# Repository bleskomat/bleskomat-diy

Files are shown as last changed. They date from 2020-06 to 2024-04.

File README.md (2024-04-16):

# Bleskomat DIY

The Bleskomat DIY is an offline Bitcoin Lightning Network ATM which accepts coins and pays-out bitcoin. It's a great educational tool to give others a practical first experience with Bitcoin's Lightning Network.

You can buy the [Bleskomat DIY kit](https://shop.bleskomat.com/product/bleskomat-diy-kit/) from the official Bleskomat shop - includes all the parts needed to build the project. Alternatively, you can find all the components and equipment needed from various other sources - see [Parts Suppliers](#parts-suppliers).

The Bleskomat DIY must be paired with a server to facilitate Lightning Network payments on its behalf; see the options below:
* [Bleskomat Platform](https://platform.bleskomat.com) - non-custodial, requires a monthly subscription
* [bleskomat-server](https://github.com/bleskomat/bleskomat-server) - non-custodial, open-source, self-hosted solution
* [lnbits](https://github.com/lnbits/lnbits-legend) via the Bleskomat extension - open-source, self-hosted and possible to use custodial instances hosted by others; public instances of lnbits:
	* [legend.lnbits.com](https://legend.lnbits.com) - unstable, don't leave funds on this instance for very long

The rest of this document details the hardware and software requirements, how to build the hardware yourself, and instructions for compiling and uploading the firmware from source.

* [Requirements](#requirements)
	* [Hardware Requirements](#hardware-requirements)
		* [Parts Suppliers](#parts-suppliers)
	* [Software Requirements](#software-requirements)
* [Building the Hardware Device](#building-the-hardware-device)
	* [Prepare the breadboards](#prepare-the-breadboards)
		* [ESP32 devkit pinout](#esp32-devkit-pinout)
	* [Wiring the Power Supply](#wiring-the-power-supply)
		* [Optionally power the ESP32 devkit via 5V pin](#optionally-power-the-esp32-devkit-via-5v-pin)
	* [Wiring the TFT Display](#wiring-the-tft-display)
		* [Wiring the SD card slot](#wiring-the-sd-card-slot)
	* [Wiring the button](#wiring-the-button)
	* [Wiring the Coin Acceptor](#wiring-the-coin-acceptor)
		* [Wiring the DG600F](#wiring-the-dg600f)
		* [Wiring the HX616](#wiring-the-hx616)
	* [Wiring the Bill Acceptor](#wiring-the-bill-acceptor)
* [Configure and Train Coin Acceptor](#configure-and-train-coin-acceptor)
	* [Configure and Train the DG600F](#configure-and-train-the-dg600f)
	* [Configure and Train the HX616](#configure-and-train-the-hx616)
* [Configure Bill Acceptor](#configure-bill-acceptor)
* [Installing Libraries and Dependencies](#installing-libraries-and-dependencies)
* [Configure Firmware Build Flags](#configure-firmware-build-flags)
* [Compiling and Uploading to Device](#compiling-and-uploading-to-device)
* [Configuring the Device](#configuring-the-device)
	* [List of Configuration Options](#list-of-configuration-options)
	* [Browser-Based Configuration Tool](#browser-based-configuration-tool)
	* [Command-Line Configuration Tool](#command-line-configuration-tool)
	* [Hard-Coded Configuration](#hard-coded-configuration)
	* [Configuration via SD Card](#configuration-via-sd-card)
* [Changelog](#changelog)
* [Support](#support)
* [License](#license)
* [Trademark](#trademark)

## Requirements

This section includes information about the software and hardware requirements needed to build this project.

### Hardware Requirements

Basic components/equipment needed to build your own Bleskomat DIY:
* 2 x breadboard (400-pin)
* Jumper wires (M-M)
* Jumper wires (M-F)
* ESP32 Devkit
* Coin Acceptor - DG600F or HX616
* 1.8" TFT display
* Button
* 10k ohm resistor
* DC 5.5/2.1 mm DIP adapter
* 12V DC power adaptor with \~1A
* Standard USB to micro USB cable
* Multimeter

Optional components/equipment:
* Soldering iron
* 2.54 mm pins
* To power the ESP32 devkit from the 12V DC power supply:
	* XL4005 step-down converter
	* USB (F) adapter
	* Alternatively, you could use a USB car charger which includes both a step-down converter and USB (F) output
* If you wish to configure your Bleskomat via SD card:
	* Micro SD card with macro adapter

See the [Parts Suppliers](#parts-suppliers) section below for links to suppliers for each component/equipment.

#### Parts Suppliers

Below are parts lists based on geographic location:

* [Czech Republic](docs/parts-lists/czech-republic.md)
* [United Kingdom](docs/parts-lists/uk.md)
* [USA](docs/parts-lists/usa.md)

If you'd like to add your own list, please create a pull-request using [this template](docs/parts-lists/TEMPLATE.md) as a guide. Links with referral codes will not be accepted.

### Software Requirements

* [make](https://www.gnu.org/software/make/)
* [PlatformIO Core (CLI)](https://docs.platformio.org/en/latest/core/)
	* Version 6 or newer
	* Only the CLI ("Core") is required

## Building the Hardware Device

Before proceeding, be sure that you have all the project's [hardware requirements](#hardware-requirements).

Step-by-step build process for the hardware device.

### Prepare the breadboards

One breadboard is not large enough to accommodate all the pins of the ESP32 devkit due to the width of the devkit. This is why we recommend to connect two breadboards together.

Remove one of the power rails from one of the breadboards. Use the notches on the sides of the breadboards to connect them together length-wise.

Insert the ESP32 devkit into the pin holes of the new, combined breadboard.

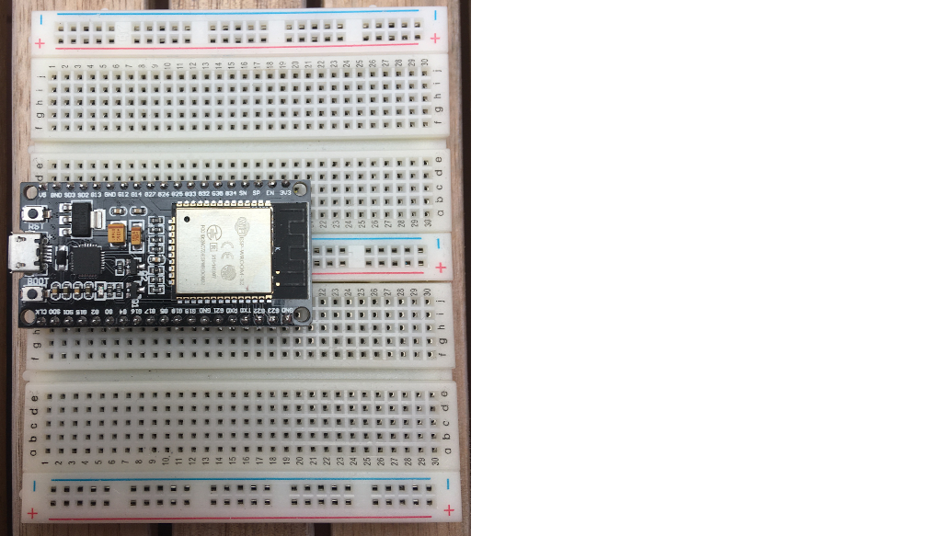
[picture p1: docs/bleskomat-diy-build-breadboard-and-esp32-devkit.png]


Familiarize yourself with the ESP32 devkit's pinout reference below.

#### ESP32 devkit pinout

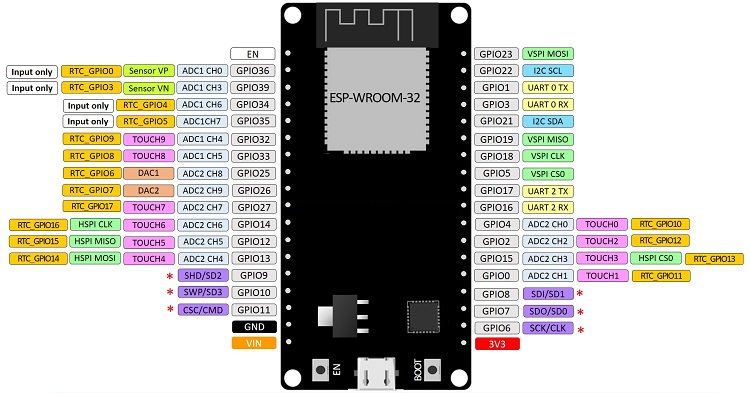
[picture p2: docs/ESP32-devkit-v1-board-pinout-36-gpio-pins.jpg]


### Wiring the Power Supply

The first step to building the device is wiring the power supply. If already plugged in, __unplug__ the 12V DC power supply now. Connect the DC 5.5/2.1 end of the power supply to the DIP adapter. The positive (+) pins should be the power pins and the negative (-) pins should be the ground. You can use your multimeter to check in case you want to be extra safe:
* Plug-in the power supply to electricity
* Turn on your multimeter and set it to measure voltage in the appropriate range (probably 20V)
* Touch the __red__ lead of your multimeter to one of the positive pins
* Touch the __black__ lead of your multimeter to one of the negative pins
* If you see a negative voltage reading, swap the leads between the two wires
* The pin touched by the __black__ lead is the ground ("GND")
* The pin touched by the __red__ lead is the hot wire ("DC12V")
* Unplug the power supply again

Use a pair of M-F jumper wires to connect the DC 5.5/2.1 DIP adapter to one of the breadboard's power rails. Negative to negative, positive to positive. This rail will be your 12V DC power (positive) and the common ground (negative).

#### Optionally power the ESP32 devkit via 5V pin

If you'd like to make your Bleskomat build a little bit more portable, you can power the ESP32 devkit via its 5V pin. To do this you will need the XL4005 (or equivalent) step-down converter and the USB (F) adapter. Note that powering the ESP32 devkit via its micro USB port requires a regulated voltage of approximately 5V.

It's also possible to use a USB car charger in case you have an extra one lying around.

Connect the step-down converter's input pins to the 12V DC power rail and common ground using (M-F) jumper wires. Use a multimeter to measure the voltage at the out pins. In the case of the XL4005, use a small screwdriver to turn the screw on the little blue box. Turning the screw counter clockwise should lower the voltage, turning it the opposite direction should increase the voltage. Once you have the voltage set to 5V, connect the out pins to the center power rails of the breadboard. This will be your 5V DC power rail.

Use a soldering iron to solder four 2.54 mm pins to the USB (F) DIP adapter. Insert the pins directly into the breadboard wherever you have space available. Using (M-M) jumper wires, connect the negative and positive pins of the USB (F) DIP adapter to the 5V DC power rail.

Connect the negative pin of the 5V DC power rail to the negative of the 12V DC power rail to ensure that they share a common ground. This is important because without a common ground shared between the coin acceptor and ESP32 devkit, the ESP32 will not receive a clean signal from the coin acceptor.

Use a standard USB to micro USB cable to connect the USB (F) DIP adapter to the ESP32 devkit.

There are other options when powering the ESP32 - e.g via the 3.3V pin or the 5V/VIN pin. You should __never__ power the ESP32 via more than one of these options at the same time. For example, do not power the ESP32 via its 3.3V pin while also connecting the ESP32 via USB to your computer. This can damage the ESP32 and possibly also your computer.

### Wiring the TFT Display

Insert the pins of the TFT display module into the breadboard where you have space available.

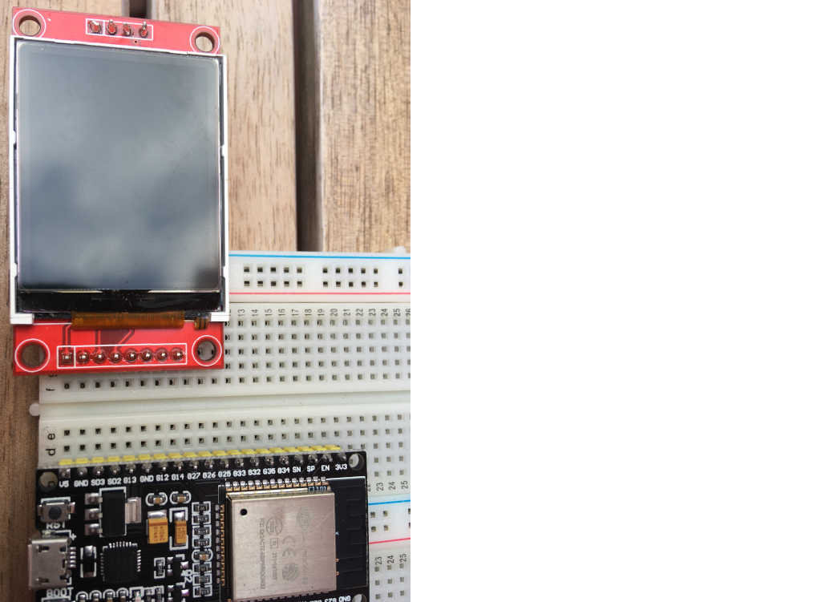
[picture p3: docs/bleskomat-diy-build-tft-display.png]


Use the table below to connect the ESP32 devkit to the TFT display module.

|  ESP32 | TFT |
|---|---|
| VIN (V5) | VCC |
| GND | GND |
| GPIO22 | CS |
| GPIO4 | RESET (RST) |
| GPIO2 | AO (RS) |
| GPIO23 | SDA |
| GPIO18 | SCK (CLK) |
| 3V3 | LED (NC) |

Notes on pin naming:
* There are boards where `GPIXXX` are marked as `GXX` instead of `DXX`.
* The `G23` may be there **twice** - the correct one is next to `GND`.
* Some boards have typos so a bit of guess-and-check is necessary sometimes.

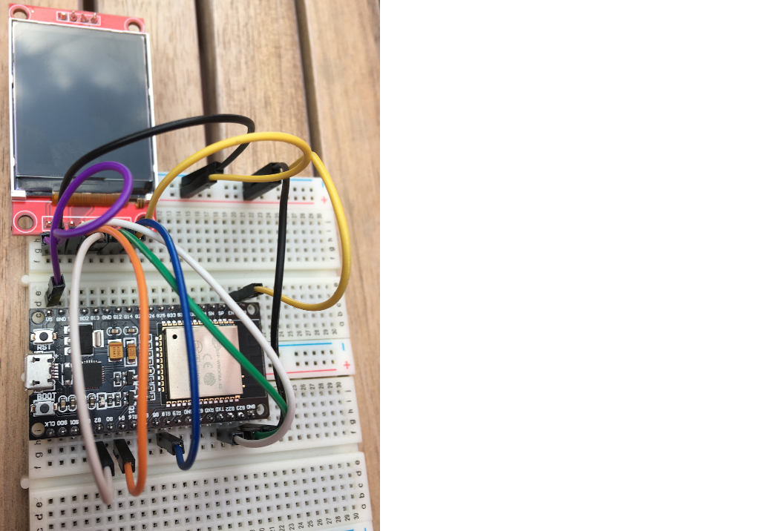
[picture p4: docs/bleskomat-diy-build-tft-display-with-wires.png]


Refer to the [ESP32 devkit pinout](#esp32-devkit-pinout) for help identifying the pins on your ESP32.

#### Wiring the SD card slot

This step is only needed if you would like to configure your Bleskomat via an SD card.

The TFT display includes an SD card slot. The pins are located above the screen and not soldered to the module by default but the pins can be added. The table of mappings is the following:

| ESP32  | TFT |
|---|---|
| GPIO15 | SD_CS |
| GPIO13 | SD_MOSI |
| GPIO12 | SD_MISO |
| GPIO14 | SD_SCK  |

Refer to the [ESP32 devkit pinout](#esp32-devkit-pinout) for help identifying the pins on your ESP32.

### Wiring the button

Insert button pins into the breadboard wherever you have space available. Typically, its best to place the button at the center of a breadboard (over the gap).

Connect the button using the following table as a guide:

| ESP32 | Button |
|---|---|
| VIN (V5) | left pin  |
| GPIO33 | right pin |

Connect the right pin of the button to GND with a 10k ohm resistor.

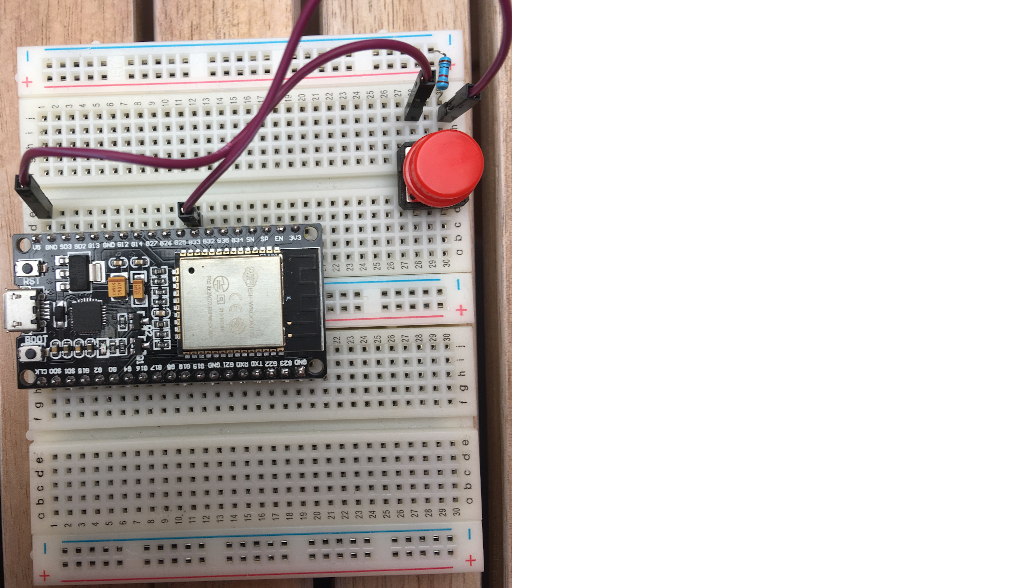
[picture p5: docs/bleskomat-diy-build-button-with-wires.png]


Refer to the [ESP32 devkit pinout](#esp32-devkit-pinout) for help identifying the pins on your ESP32.

### Wiring the Coin Acceptor

This project supports two possible coin acceptors - the DG600F and the HX616. The DG600F is more expensive, but is easier to configure and more reliable.

#### Wiring the DG600F

| ESP32 | DG600F | Power Supply  |
|---|---|---|
| GPIO1 (TX0) | INHIBIT  | |
| | COUNTER  | |
| | GND | - Ground |
| GPIO3 (RX0) | SIGNAL | |
| | DC12V | + 12V DC |

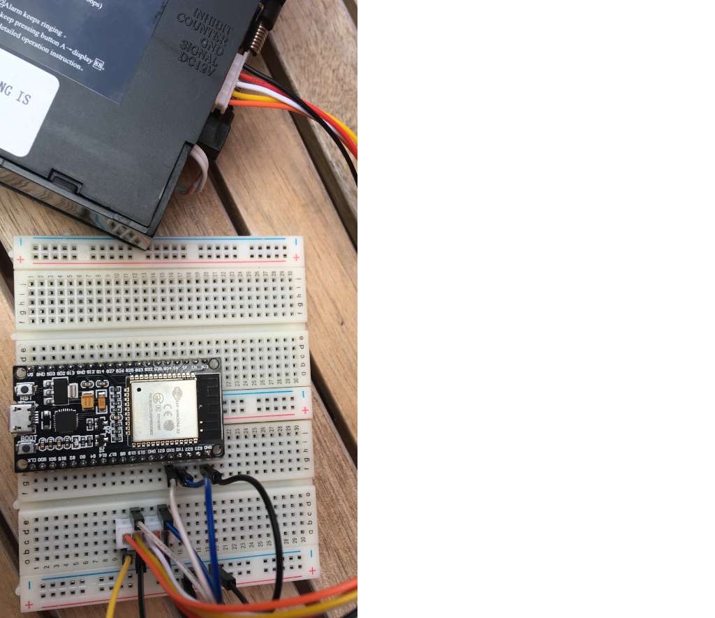
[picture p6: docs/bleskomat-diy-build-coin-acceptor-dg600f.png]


Refer to the [ESP32 devkit pinout](#esp32-devkit-pinout) for help identifying the pins on your ESP32.

#### Wiring the HX616

| ESP32 | HX616 | Power Supply  |
|---|---|---|
| | DC12V | + 12V DC |
| GPIO3 (RX0) | COIN | |
| | GND | - Ground |

Refer to the [ESP32 devkit pinout](#esp32-devkit-pinout) for help identifying the pins on your ESP32.

### Wiring the Bill Acceptor

This project supports the NV10 (USB+) and NV9 bill acceptors. The SIO protocol is used to communicate with the bill acceptor unit.

|  ESP32 | NV10/NV9 | Power Supply  |
|---|---|---|
| GPIO16 | 1 (Tx) | |
| GPIO17 | 5 (Rx) | |
| | 16 | - Ground |
| | 15 | + 12V DC |

Refer to the [ESP32 devkit pinout](#esp32-devkit-pinout) for help identifying the pins on your ESP32.

## Configure and Train Coin Acceptor

This project supports two possible coin acceptors - the DG600F and the HX616.

### Configure and Train the DG600F

Physical switches on the DG600F should set as follows:

| Switch | State |
|---|---|
| 1 (Port Level) | Down (NO) |
| 2 (Security) | Down (Normal) |
| 3 (Transmitting) | Up (RS232) |
| 4 (Inhibiting) | Down (> +3V)  |



Open the [DG600F manual](docs/DG600F-Coin-Acceptor-Technical-Manual.pdf) to "Coin Acceptor Parameters Setting" on page 18. Set the parameters as follows:

| Parameter | Description | Value | Meaning |
|---|---|---|---|
| A1 | machine charge amount | 01 | min. coin value before data sent |
| A2 | serial output signal pulse-width | 01 | 25ms / 9600 bps (RS232 baud rate) |
| A3 | faulty alarm option | 01 | (rings only one time) |
| A4 | serial port RS232 signal length  | 03 | 3 bytes: 0xAA, coin value, XOR of prev two bytes |
| A5 | serial port output | 01 | output to serial pin |

To train the coin acceptor, have a look at "Coin Parameters Setting" on page 16 of the [DG600F manual](docs/DG600F-Coin-Acceptor-Technical-Manual.pdf). Be sure to set the "coin value" for each coin in series, incremented by 1. For example:
* 0.05 EUR = 1 coin value
* 0.10 EUR = 2 coin value
* 0.20 EUR = 3 coin value
* 0.50 EUR = 4 coin value
* 1.00 EUR = 5 coin value
* 2.00 EUR = 6 coin value

Then set the `coinValues` configuration equal to `0.05,0.10,0.20,0.50,1,2`. For example, in the bleskomat.conf:
```
coinValues=0.05,0.10,0.20,0.50,1,2
```

### Configure and Train the HX616

There are two switches on the back of the HX616 coin acceptor:
* "NO" (normally open) / "NC" (normally closed) - This should be set to "NO"
* "Fast" / "Medium" / "Slow" - This should be set to "Fast"

An instruction sheet is included with the coin acceptor that will guide you through the training process:

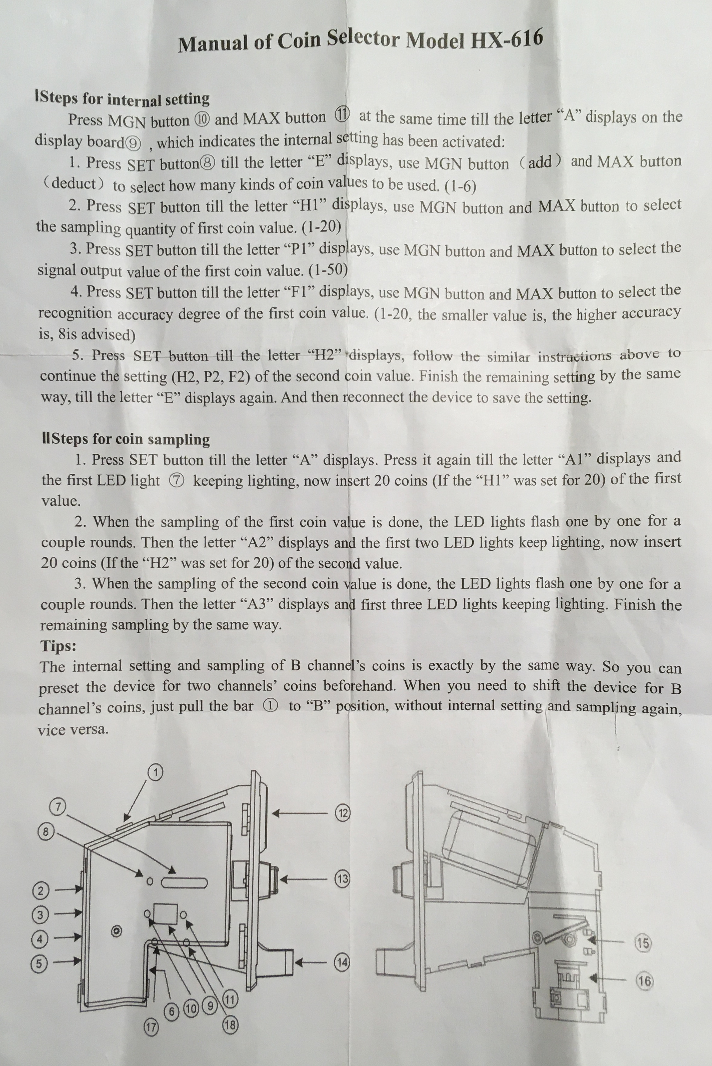
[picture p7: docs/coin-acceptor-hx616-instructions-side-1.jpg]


| PANEL  | Meaning |
|---|---|
| E | number of coin values |
| Hn | sampling quantity of coin n |
| Pn | signal output value of coin n |
| Fn | recognition accuracy of coin n (8 advised)  |
| A | training the acceptor |
| An | start inserting coins for coin n |

Press ADD + MINUS to get to the setting menu for Hn, Pn, Fn. Then press SET to swap between possibilities. To change the option press ADD or MINUS to select the desired value and confirm with SET.

Press SET to enter the training menu (A appears on the panel). After pressing SET again you can start inserting the coins.

If training the HX616 to accept EUR coins, you can set the `coinValueIncrement` equal to `0.05`. For example, in bleskomat.conf:
```
coinValueIncrement=0.05
```

## Configure Bill Acceptor

Please refer to the following user manuals for detailed instructions regarding how to configure the NV10 (USB+) or NV9 bill acceptors:
* [NV10 User Manual](docs/NV10-User-Manual-v1.1.pdf)
* [NV9 User Manual](docs/NV9-User-Manual-v1.1.pdf)

## Installing Libraries and Dependencies

Before proceeding, be sure that you have all the project's [software requirements](#software-requirements).

Use make to install libraries and dependencies needed to build the firmware:
```bash
make install
```
* The firmware's dependencies are defined in its platformio.ini file located at `./platformio.ini`

If while developing you need to install a new library, use the following as a guide:
```bash
platformio lib install LIBRARY_NAME[@VERSION]
```
You can find PlatformIO's libraries repository [here](https://platformio.org/lib).

## Configure Firmware Build Flags

There are several build flags that can be changed in file platformio.ini file located at `./platformio.ini` before the firmware is compiled. If you follow the wire mappings in this readme file, then you most likely do not need to change any flags.

## Compiling and Uploading to Device

To compile the firmware (without uploading to a device):
```bash
make compile
```

To compile and upload to your device:
```bash
make upload DEVICE=/dev/ttyUSB0
```
The device path for your operating system might be different. If you receive a "Permission denied" error about `/dev/ttyUSB0` then you will need to set permissions for that file on your system:
```bash
sudo chown $USER:$USER /dev/ttyUSB0
```

To open the serial monitor:
```bash
make monitor DEVICE=/dev/ttyUSB0
```
Again the device path here could be different for your operating system.

## Configuring the Device

It is possible to configure the device via the following methods:
* [Browser-Based Configuration Tool](#browser-based-configuration-tool)
* [Command-Line Configuration Tool](#command-line-configuration-tool)
* [Hard-Coded Configuration](#hard-coded-configuration)
* [Configuration via SD Card](#configuration-via-sd-card)

### List of Configuration Options

The following is a list of possible configuration options for the Bleskomat DIY:
* `apiKey.id` - The API key ID of the device. This is needed by the server to verify signatures created by the device.
* `apiKey.key` - The API key secret that is used to generate signatures.
* `apiKey.encoding` - The explicit encoding of the API key secret. This can be "hex", "base64", or empty-string (e.g "") to mean no encoding. When generating a new API key on the server, it will store the encoding along with the ID and secret.
* `callbackUrl` - The LNURL server base URL plus endpoint path. Example:
	* `https://p.bleskomat.com/u`
* `shorten` - Whether or not to shorten the LNURL; see the [lnurl-node module](https://github.com/chill117/lnurl-node#signed-lnurls) for more details.
* `uriSchemaPrefix` - The URI schema prefix for LNURLs generated by the device. It has been discovered that some wallet apps mistakenly only support lowercase URI schema prefixes. Uppercase is better because when encoded as a QR code, the generated image is less complex and so easier to scan. Set this config to empty-string (e.g `uriSchemaPrefix=`) to not prepend any URI schema prefix.
* `fiatCurrency` - The fiat currency symbol for which the device is configured; see [ISO 4217](https://en.wikipedia.org/wiki/ISO_4217).
* `fiatPrecision` - The number of digits to the right of the decimal point when rendering fiat currency amounts.
* `billValues` - The value of bills for which the bill acceptor has been configured. Each value separated by a comma. Integers and floating point (decimal) values are accepted. Examples:
	* CZK: `100,200,500,1000,2000,5000`
	* EUR: `5,10,20,50,100,200,500`
* `billTxPin` - The GPIO connected to the NV10/NV9's Tx pin.
* `billRxPin` - The GPIO connected to the NV10/NV9's Rx pin.
* `billBaudRate` - The baud rate of the SIO protocol communication with the NV10/NV9. This value will be `300` or `9600`.
* `coinValues` - For the DG600F coin acceptor. The value of coins for which the coin acceptor has been configured. Each value separated by a comma. Integers and floating point (decimal) values are accepted. For example, when trained with EUR coins this configuration could be set to `0.05,0.10,0.20,0.50,1,2`.
* `coinValueIncrement` - For the HX616 coin acceptor, which communicates via pulses to the ESP32. The value here will determine how much fiat value each pulse represents. For example, when trained with EUR coins this value could be `0.05` with the following number of pulses set for each coin denomination:
	* 0.05 EUR = 1 pulse
	* 0.10 EUR = 2 pulses
	* 0.20 EUR = 4 pulses
	* 0.50 EUR = 10 pulses
	* 1.00 EUR = 20 pulses
	* 2.00 EUR = 40 pulses
* `coinSignalPin` - The GPIO connected to the HX616's "COIN" pin or DG600F's "SIGNAL" pin.
* `coinInhibitPin` - The GPIO connected to the DG600F's "INHIBIT"
* `coinBaudRate` - The baud rate for serial communication with the DG600F
* `coinAcceptorType` - "hx616" or "dg600f"
* `buttonPin` - The GPIO connected to the button
* `buttonDelay` - The number of milliseconds to wait before pressing the button can clear the QR code
* `buttonDebounce` - The number of milliseconds of debounce to prevent flickering button press/release
* `tftRotation` - The orientation of the TFT display. This is useful to allow different positions of the display. The possible rotation values are:
	* 0 = 0 degrees
	* 1 = 90 degrees
	* 2 = 180 degrees
	* 3 = 270 degrees
* `logLevel` - Possible values:
	* `trace` - everything
	* `debug`
	* `info` - default
	* `warn`
	* `error`
	* `none` - nothing

### Browser-Based Configuration Tool

The Bleskomat Platform provides a [browser-based configuration tool](https://platform.bleskomat.com/serial) to upload pre-built device firmware, view real-time log output, update device configurations, run JSON-RPC serial commands, and more.

### Command-Line Configuration Tool

It is also possible to use the [bleskomat-cli](https://github.com/bleskomat/bleskomat-cli) command-line utility to communicate with a Bleskomat hardware device via JSON-RPC over serial API. Please refer to that project's readme for installation and usage information.

### Hard-Coded Configuration

Hard-coded configurations can be set by modifying the source file [config.cpp](https://github.com/bleskomat/bleskomat-diy/blob/master/src/config.cpp#L196).

Each time you make changes to the hard-coded configurations, you will need to re-compile and flash the ESP32's firmware.

### Configuration via SD Card

First you will need to format the SD card with the FAT32 filesystem.

Create a new file named `bleskomat.conf` at the root of the SD card's filesystem.

The following is an example `bleskomat.conf` file:
```
apiKey.id=6d830ddeb0
apiKey.key=b11cd6b002916691ccf3097eee3b49e51759225704dde88ecfced76ad95324c9
apiKey.encoding=hex
callbackUrl=https://p.bleskomat.com/u
shorten=true
uriSchemaPrefix=
fiatCurrency=EUR
fiatPrecision=2
coinValues=0.05,0.10,0.20,0.50,1,2
coinValueIncrement=0.05
coinSignalPin=3
coinInhibitPin=1
coinBaudRate=9600
coinAcceptorType=hx616
buttonPin=33
buttonDelay=5000
buttonDebounce=100
tftRotation=2
logLevel=info
```

## Changelog

See [CHANGELOG.md](https://github.com/bleskomat/bleskomat-diy/blob/master/CHANGELOG.md)

## Support

Need some help? Join us in the official [Telegram group](https://t.me/bleskomat) or send us an email at [support@bleskomat.com](mailto:support@bleskomat.com) and we will try our best to respond in a reasonable time. If you have a feature request or bug to report, please [open an issue](https://github.com/bleskomat/bleskomat-diy/issues) in this project repository.

## License

The project is licensed under the [GNU General Public License v3 (GPL-3)](https://tldrlegal.com/license/gnu-general-public-license-v3-(gpl-3)):
> You may copy, distribute and modify the software as long as you track changes/dates in source files. Any modifications to or software including (via compiler) GPL-licensed code must also be made available under the GPL along with build & install instructions.

## Trademark

"Bleskomat" is a registered trademark. You are welcome to hack, fork, build, and use the source code and instructions found in this repository. However, the right to use the name "Bleskomat" with any commercial products or services is withheld and reserved for the trademark owner.

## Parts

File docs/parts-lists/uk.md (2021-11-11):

# Parts List for United Kingdom

List of recommended electronics parts suppliers in UK:
* [Hobbytronics](https://www.hobbytronics.co.uk/)
* [RobotShop](https://www.robotshop.com/uk/)
* [AdaptorsRUs](https://www.acadaptorsrus.co.uk/)
* [RSComponents](https://uk.rs-online.com/web/)
* [HobbyComponents](https://hobbycomponents.com/)
* [PicStop](https://www.picstop.co.uk/)

Basic components/equipment needed to build your own Bleskomat (DIY) ATM:
* 2 x [Breadboard (400-pin)](https://www.hobbytronics.co.uk/breadboard-400)
* [Connecting cables (M-M)](https://www.hobbytronics.co.uk/jumper-wires-mm-6in)
* [Connecting cables (M-F)](https://www.hobbytronics.co.uk/jumper-wires-mf-6in)
* [ESP32 Devkit](https://www.robotshop.com/uk/esp32-c3-devkitc-02-development-board.html)
* [DG600F Coin Acceptor](https://www.robotshop.com/uk/programmable-coin-acceptor.html)
* [1.8" TFT display](https://www.robotshop.com/uk/sparkfun-18-128x160-tft-lcd-breakout-board.html)
* [Button](https://www.hobbytronics.co.uk/tactile-button-assortment)
* [10k ohm resistor](https://www.robotshop.com/uk/resistor-10k-ohm-1-4-watt-pth-20pk.html)
* [DC 5.5/2.1 mm DIP adapter](https://www.ebay.co.uk/itm/DC-Power-Jack-with-DIP-Adapter-Barrel-Type-Socket-Breakout-Board-DC-Power-Supply-/114944864538)
* [12V DC power adaptor with \~1A](https://www.acadaptorsrus.co.uk/12v-1a-1-amp-mains-ac-dc-adaptor-power-supply-for-yeskamo-cctv-system-uk-plug/) or [this one](https://uk.rs-online.com/web/p/ac-dc-adapters/1753303/)
* [Standard USB to micro USB cable](https://uk.rs-online.com/web/p/usb-cables/1828869)
* [Multimeter](https://www.hobbytronics.co.uk/digital-multimeter-basic)

Optional components/equipment:
* [Soldering iron](https://www.hobbytronics.co.uk/test-equipment/soldering_tools/antex-soldering-iron-xs25)
* [2.54 mm pins](https://hobbycomponents.com/connectors/656-ra-40-way-01-breakable-male-pin-headers)
* To power the ESP32 devkit from the 12V DC power supply:
	* [DC-DC step-down converter](https://www.robotshop.com/uk/step-down-dc-dc-power-converter-25w.html)
	* [USB (F) adapter](https://www.hobbytronics.co.uk/cables-connectors/usb-connectors/usb-type-a-socket)
	* Alternatively, you could use a USB car charger which includes both a step-down converter and USB (F) output
* If you wish to configure your Bleskomat via SD card:
	* [Micro SD card ...](https://www.picstop.co.uk/microsd-sdhc/sandisk-ultra-micro-sdhc-memory-card-98mbs-class-10-for-android-16gb.html)
	* [... with macro adapter](https://www.picstop.co.uk/card-adapters/micro-sd-card-adapter.html)

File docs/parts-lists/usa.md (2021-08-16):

# Parts List for USA

Recommended websites to search for parts:
* [digikey](https://www.digikey.com/en/products)
* [mouser](https://www.mouser.com/)

Basic components/equipment needed to build your own Bleskomat (DIY) ATM:
* 2 x [Breadboard (400-pin)](https://www.adafruit.com/product/4539)
* [Jumper wires (M-M)](https://www.adafruit.com/product/1956)
* [Jumper wires (M-F)](https://www.adafruit.com/product/825)
* ESP32 Devkit:
	* [digikey](https://www.digikey.com/en/products/detail/espressif-systems/ESP32-DEVKITC-32E/12091810)
	* [adafruit](https://www.adafruit.com/product/4693)
* DG600F Coin Acceptor:
	* [sparkfun](https://www.sparkfun.com/products/11636)
	* [alibaba](https://www.alibaba.com/trade/search?fsb=y&IndexArea=product_en&CatId=&SearchText=DG600F)
* 1.8" (128 x 160 pixel) TFT display
* [Button](https://www.adafruit.com/product/1009)
* [10k ohm resistor](https://www.adafruit.com/product/2784)
* [DC 5.5/2.1 mm DIP adapter](https://www.adafruit.com/product/798)
* [12V DC power adaptor with \~1A](https://www.adafruit.com/product/798)
* Standard USB to micro USB cable
* [Multimeter](https://www.adafruit.com/product/2034)

Optional components/equipment:
* [Soldering iron](https://www.adafruit.com/product/180)
* 2.54 mm pins
* To power the ESP32 devkit from the 12V DC power supply:
	* XL4005 step-down converter
	* USB (F) adapter
	* Alternatively, you could use a USB car charger which includes both a step-down converter and USB (F) output
* If you wish to configure your Bleskomat via SD card:
	* Micro SD card with macro adapter

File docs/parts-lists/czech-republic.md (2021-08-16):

# Parts List for Czech Republic

List of recommended electronics parts suppliers in Czech Republic:
* [laskarduino.cz](https://www.laskarduino.cz)
* [alza.cz](https://www.alza.cz)
* [gme.cz](https://www.gme.cz/)

Basic components/equipment needed to build your own Bleskomat (DIY) ATM:
* 2 x [Breadboard (400-pin)](https://www.laskarduino.cz/nepajive-kontaktni-pole-400-pinu--bile/)
* [Jumper wires (M-M)](https://www.laskarduino.cz/dupont-propojovaci-kabely-40ks-m-m-samec-samec--10cm-/)
* [Jumper wires (M-F)](https://www.laskarduino.cz/dupont-propojovaci-kabely-40ks-m-f-samec-samice--10cm-/)
* [ESP32 Devkit](https://www.laskarduino.cz/iot-esp-32s-2-4ghz-dual-mode-wifi-bluetooth-rev-1--cp2102/)
* DG600F Coin Acceptor:
	* _No known local part supplier_
	* Suggestions:
		* [Alibaba.com](https://www.alibaba.com/trade/search?fsb=y&IndexArea=product_en&CatId=&SearchText=DG600F)
		* [Sparkfun.com](https://www.sparkfun.com/products/11636)
* [1.8" TFT display](https://www.laskarduino.cz/128x160-barevny-lcd-tft-displej-1-8--spi/)
* [Button](https://www.laskarduino.cz/mikrospinac-tc-1212t-12x12x7-3mm/)
* [10k ohm resistor](https://www.laskarduino.cz/futaba-1-4w-odpor-10k-5/)
* [DC 5.5/2.1 mm DIP adapter](https://www.laskarduino.cz/dc-5-5-2-1mm-na-dip-adapter-led/)
* [12V DC power adaptor with \~1A](https://www.laskarduino.cz/napajeci-adapter-sitovy-1000ma-5-5-2-1-mm-12v/)
* [Standard USB to micro USB cable](https://www.laskarduino.cz/50cm-microusb-kabel/)
* [Multimeter](https://www.gme.cz/digitalni-multimetr-proskit-mt-1210)

Optional components/equipment:
* [Soldering iron](https://www.gme.cz/pajeci-stanice-48w-ss-203b)
* [2.54 mm pins](https://www.laskarduino.cz/dupont-40pin-2-54-mm-pinovy-pas--pravy-uhel/)
* To power the ESP32 devkit from the 12V DC power supply:
	* [XL4005 step-down converter](https://www.laskarduino.cz/step-down-menic-s-xl4005/)
	* [USB (F) adapter](https://www.laskarduino.cz/usb-f-na-dip-adapter/)
	* Alternatively, you could use a USB car charger which includes both a step-down converter and USB (F) output
* If you wish to configure your Bleskomat via SD card:
	* [Micro SD card with macro adapter](https://www.alza.cz/sandisk-microsdhc-16gb-ultra-android-class-10-uhs-i-d5127467.htm?o=2)

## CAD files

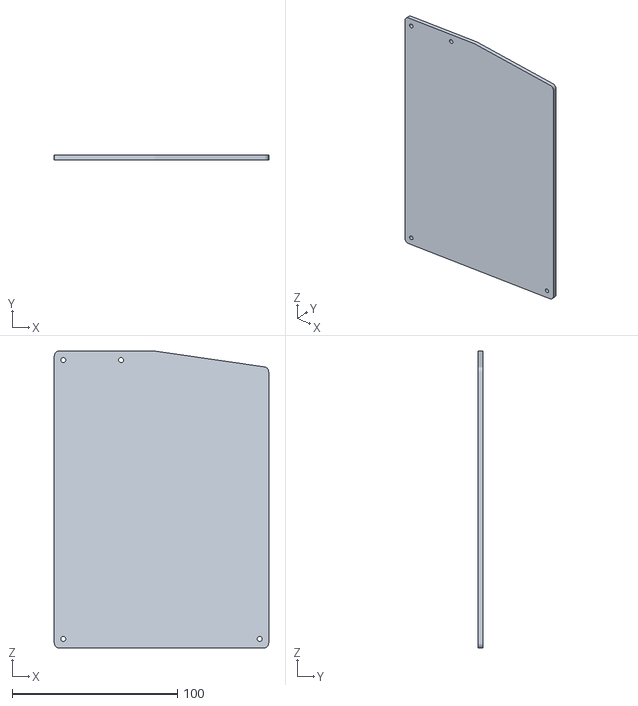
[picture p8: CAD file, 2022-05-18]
case/hx616/door.stl
130.0 x 3.00 x 180.0

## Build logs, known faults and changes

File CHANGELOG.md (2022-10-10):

# Changelog

* v1.3.0:
	* Bill acceptor support
	* Debounce hx616 pulse counting to prevent extraneous accumulated value. Don't count pulses caused by reconnecting coin signal pin, or when powering on the hx616, or when changing the physical switches on the hx616. Still possible but less likely as pulse high/low must be 20-200ms.
	* Fix QR code too small when text_size increased
* v1.2.5:
	* Improved reliability of counting pulses with hx616 coin acceptor
	* Fix for non-integer coin increment value
	* Disinhibit DG600F after initialization
* v1.2.4:
	* Better initialization state handling
* v1.2.3:
	* Fix getInt/Short/Float config value when set to empty-string
* v1.2.2:
	* Added spiffsFormatted config flag
	* Return spiffsInitialized flag in getinfo JSON-RPC command
	* Send response for restart JSON-RPC command
* v1.2.1:
	* Smaller log file size
* v1.2.0:
	* Use SPIFFS file system to store logs
	* JSON-RPC via serial - echo, getconfig, setconfig, getlogs, deletelogs, spiffs_reformat, restart
	* Move coin/button build flags to configuration options
	* Button delay no longer blocks the application loop

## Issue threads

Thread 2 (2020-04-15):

Review and improve step-by-step build docs

chill117, 2020-04-15:
* [x] Review pin labeling (TFT screen to arduino) -- some of the pin labels are different on my screen/arduino
* [x] Explain how to connect the coin acceptor to the arduino
* [x] Explain how to build the power supply for the coin acceptor

Cable mappings:
* [x] Cable mapping for ESP32 to coin acceptor
* [x] Cable mapping for ESP32 to TFT screen
* ~Cable mapping for ESP32 w/ button~

chill117, 2020-06-30:
Done

Closed 2020-06-30.

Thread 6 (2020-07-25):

/bin/sh: 1: platformio: not found

ArbenKarb, 2020-07-25:
$ platformio --version
$ PlatformIO, version 4.3.4

Added path to bashrc

followed all steps

$ cd /bleskomat/bleskomat
$ sudo make install

cd ./device && platformio lib install
/bin/sh: 1: platformio: not found
make: *** [Makefile:52: install] Error 127

chill117, 2020-07-26:
Try without `sudo`:
```bash
make install
```

ArbenKarb, 2020-07-28:
Tried that, I get a permission error:

Error: Traceback (most recent call last):
  File "/home/admin/.local/lib/python3.8/site-packages/platformio/__main__.py", line 109, in main
    cli()  # pylint: disable=no-value-for-parameter
  File "/home/admin/.local/lib/python3.8/site-packages/click/core.py", line 829, in __call__
    return self.main(*args, **kwargs)
  File "/home/admin/.local/lib/python3.8/site-packages/click/core.py", line 782, in main
    rv = self.invoke(ctx)
  File "/home/admin/.local/lib/python3.8/site-packages/platformio/commands/__init__.py", line 44, in invoke
    return super(PlatformioCLI, self).invoke(ctx)
  File "/home/admin/.local/lib/python3.8/site-packages/click/core.py", line 1259, in invoke
    return _process_result(sub_ctx.command.invoke(sub_ctx))
  File "/home/admin/.local/lib/python3.8/site-packages/click/core.py", line 1259, in invoke
    return _process_result(sub_ctx.command.invoke(sub_ctx))
  File "/home/admin/.local/lib/python3.8/site-packages/click/core.py", line 1066, in invoke
    return ctx.invoke(self.callback, **ctx.params)
  File "/home/admin/.local/lib/python3.8/site-packages/click/core.py", line 610, in invoke
    return callback(*args, **kwargs)
  File "/home/admin/.local/lib/python3.8/site-packages/click/decorators.py", line 21, in new_func
    return f(get_current_context(), *args, **kwargs)
  File "/home/admin/.local/lib/python3.8/site-packages/platformio/commands/lib.py", line 151, in lib_install
    lm = LibraryManager(storage_dir)
  File "/home/admin/.local/lib/python3.8/site-packages/platformio/managers/lib.py", line 40, in __init__
    super(LibraryManager, self).__init__(
  File "/home/admin/.local/lib/python3.8/site-packages/platformio/managers/package.py", line 604, in __init__
    os.makedirs(self.package_dir)
  File "/usr/local/lib/python3.8/os.py", line 211, in makedirs
    makedirs(head, exist_ok=exist_ok)
  File "/usr/local/lib/python3.8/os.py", line 211, in makedirs
    makedirs(head, exist_ok=exist_ok)
  File "/usr/local/lib/python3.8/os.py", line 221, in makedirs
    mkdir(name, mode)
PermissionError: [Errno 13] Permission denied: '/bleskomat/bleskomat/device/.pio'

chill117, 2020-07-29:
> File "/usr/local/lib/python3.8/os.py", line 221, in makedirs mkdir(name, mode)
> PermissionError: [Errno 13] Permission denied: '/bleskomat/bleskomat/device/.pio'

Looks like your current user lacks permission to create a new directory. Try this:
```bash
sudo chmod -R 0755 ./
```

ArbenKarb, 2020-08-01:
thanks

Closed 2020-08-01.

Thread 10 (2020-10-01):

Read config options from SD card

chill117, 2020-10-01:
It is a bit annoying to need to compile and upload the firmware every time configuration options are changed. It could be better to write the configs to an SD card instead.

Most of the TFT displays come with an SD card reader - usually 4 extra pins that need to be connected to the ESP32. There are already libraries available in [platformio](https://platformio.org/lib) that can read from the SD card.

Bonus points for encrypting the config data on the SD card using asymmetric cryptography (public key on the server, private key on the device compiled in its firmware).

chill117, 2020-11-14:
Done by #14

Closed 2020-11-15.

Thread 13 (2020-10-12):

Invalid API key signature

joetinker, 2020-10-12:
Please help me with resolving this error. HW "Beskomat" works, but after scanning QR wallet reports:

	Error message from remote provider: Invalid API key signature

Thanks

chill117, 2020-10-12:
Hello @joetinker. Where do you see that error? In the mobile wallet when attempting to scanning a QR code displayed on your TFT? Or do you see the error in your terminal window that is running the server?

joetinker, 2020-10-13:
Yes, in the mobile wallet (BLW or WoS) when attempting to scan a QR code displayed on Bleskomat. I generate key by "lnurl generateApiKey" on the server and in include id & key to the Bleskomat firmware.
The terminal window shows "lnurl:request GET /api?id=1bd03af8f5&n=1513154355&t=w&f=CZK&pn=1&px=1&pd=&s=645c0f7673ae25d93a8d09434ad96fa8a2e1a11f2acc1f16378aad53fbad53f6 +7m"

chill117, 2020-10-14:
> I generate key by "lnurl generateApiKey" on the server and in include id & key to the Bleskomat firmware

Did you put that API key in your server's config.json? It should be at `lnurl.auth.apiKeys` as an element of an array. For example:
```js
{
	"lnurl": {
		// ...
		"auth": {
			"apiKeys": [
				{
					"id": "rp/hlgc=",
					"key": "QA0ClaLFSjnsfybL8apu3YsDkvPAm8F9hq3bE8ZkNYw="
				}
			]
		}
	}
}
```
It might be necessary to use base64 encoded API key ID/Secret with the current device firmware because of how the device does the signing.

Try generating a new API key as follows:
```bash
lnurl generateApiKey --encoding "base64"
```
And add it to your server's config.

joetinker, 2020-10-14:
Thank you so much for the support, [ lnurl generateApiKey --encoding "base64" ] probably helped. I created a new id / key and transferred it on to another server using scp. Before that I transferred id / key via Windows clipboard, so maybe there was a change the encoding.

Closed 2020-10-15.

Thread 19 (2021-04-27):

Board is not counting accepted coins

martinkuchar2, 2021-04-27:
I have built my first Bleskomat, it is on and running (I can see 0 Kc on display) and the coin acceptor is programmed on and accepting coins (can see the right number on its display). But the device still shows 0 Kc event after inserting coins - looks like it can not accept signals from the acceptor. Please, can you help me to get this fixed? All grounds are connected in the right way (like on the diagram)... Thanks

chill117, 2021-04-27:
Have you seen these notes from the README file?
> There are two switches on the back of the HX-616 coin acceptor:
> * "NO" (normally open) / "NC" (normally closed) - This should be set to "NO"
> * "Fast" / "Medium" / "Slow" - This should be set to "Fast"

If these switches are not set as described here, then the pulses won't be sent in a way that the ESP32 can understand.

martinkuchar2, 2021-04-27:
Sure, this is set as it should be to NO and Fast. Any other idea, please?

chill117, 2021-04-27:
Do you have a shared ground between the ESP32 and the coin acceptor?

martinkuchar2, 2021-06-23:
> We've made some updates to the firmware and components list. The coin acceptor has been changed to the DG600F which is much more reliable than the previously used coin acceptor. Please refer to the latest project readme for details.

Please do you have a diagram of older version with 616 acceptor please? Can not find it here any more. Thanks

chill117, 2021-06-23:
You can find the old documentation here:
https://github.com/samotari/bleskomat-diy/tree/eccf6d46e87672ea28d633a8c26bc4cbd1c8c133

Closed 2021-06-23.

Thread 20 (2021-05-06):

missing repo during make install

rmoh795, 2021-05-06:
Hi,
i'm trying to compile the bleskomat, but when i try to do so, i get error:

remote: Repository not found.
fatal: repository 'https://github.com/chill1/lnurl/' not found

And this repo is indeed unavailable. Is there any workaround please?
Thank you

chill117, 2021-05-07:
Which command do you run when you see the error?

rmoh795, 2021-05-07:
It happens during Installing Libraries and Dependencies, when I run `make install` to install all dependencies and libraries. I am asked to enter my github login and then I get this error, that the repository is not found.

chill117, 2021-05-07:
Can you please copy/paste the output that you are seeing when you run the `make install` command?

rmoh795, 2021-05-07:
`└─$ make install
cd ./device && platformio lib install
Library Storage: /home/user/Downloads/bleskomat-master/device/.pio/libdeps/bleskomat32
Looking for QRCode library in registry
Found: https://platformio.org/lib/show/1584/QRCode
LibraryManager: Installing id=1584 @ ^0.0.1
Using cache: /home/user/.platformio/.cache/e0/a4f1df25d468f09ebf2172c2033e85e0
QRCode @ 0.0.1 has been successfully installed!
Looking for TFT_eSPI library in registry
Found: https://platformio.org/lib/show/1559/TFT_eSPI
LibraryManager: Installing id=1559 @ ^2.2.6
Using cache: /home/user/.platformio/.cache/a2/12c42a822a24e2b336495dd8f584ada2
Unpacking  [####################################]  100%
TFT_eSPI @ 2.3.67 has been successfully installed!
LibraryManager: Installing lnurl @ 0.1.3
git version 2.30.2
Cloning into '/home/user/Downloads/bleskomat-master/device/.pio/libdeps/bleskomat32/_tmp_installing-jcchocr7-package'...
Username for 'https://github.com': rmoh795
Password for 'https://rmoh795@github.com':
remote: Repository not found.
fatal: repository 'https://github.com/chill1/lnurl/' not found
Error: VCS: Could not process command ['git', 'clone', '--recursive', '--depth', '1', 'https://github.com/chill1/lnurl', '/home/user/Downloads/bleskomat-master/device/.pio/libdeps/bleskomat32/_tmp_installing-jcchocr7-package']
make: *** [Makefile:58: install] Error 1``

chill117, 2021-05-07:
And which version of platformio are you running? Run the following to print the version:
```bash
platformio --version
```

chill117, 2021-05-07:
It looks like platformio is not even trying to pull the lnurl lib from the platformio registry - it looks to be going straight to GitHub. Try changing the line in [platformio.ini](
https://github.com/samotari/bleskomat/blob/master/device/platformio.ini#L62):
```
	chill1/lnurl@0.1.3
```
To:
```
	lnurl@0.1.3
```
Then try the install again. I'm guessing you're running an old version of platformio that doesn't recognize the namespace syntax.

chill117, 2021-05-07:
> But now, when I proceed with make compile I get error, that unknown package 'espressif32' is detected. Maybe it is caused by the version of platformio I have installed.

Yes, this is possible. If you are able to upgrade your platformio version, that might be the best solution.

rmoh795, 2021-05-07:
This issue has been resolved by removing the platformio installed by apt and by installation of the latest version of platformio (Instructions here: https://docs.platformio.org/en/latest/core/installation.html#installation-methods).

Closed 2021-05-07.

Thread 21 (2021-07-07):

Support bills acceptor

iBobik, 2021-07-07:
Coins does not make sence for my use-case. I saw bills acceptor on some photos.

Does this project support it?
Are there some docs about it?

chill117, 2021-07-08:
Hello. You are correct in that this repo does not currently include support for a bill acceptor. We may add support for it during the second half of this year, but no guarantees. Until then you are welcome to fork and extend this project with a bill acceptor of your own - there are a few options available from online market places.

chill117, 2022-08-21:
@iBobik Support for the NV10 (USB+) and NV9 bill acceptors has been added by 6105a40e6dd995de38533d95790aa5229d335d9b and will be included in a future release.

chill117, 2024-04-16:
Closing because bill acceptor support was added.

Closed 2024-04-16.

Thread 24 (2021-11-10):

DG600F serial communication. Not counting coins

relcead, 2021-11-10:
Hello. We build your project. It works really nice. Thank you for sharing it with us.
While building with your recent guide we noticed serial communication errors with DG600F.

in the file: coin-acceptor.cpp
in the original line 77: Serial2.begin(COIN_ACCEPTOR_BAUDRATE, SERIAL_8N1, COIN_ACCEPTOR_SIGNAL, 0);

we had to change to:
line 77: Serial2.begin(COIN_ACCEPTOR_BAUDRATE, SERIAL_8E1, COIN_ACCEPTOR_SIGNAL, 0);

because serial communication in DG600F Manual:
S：Start bit
B0 to B7：8 data bits
C：Even check
STOP：Stop bit
It can set the transmit rate（1200bps/2400bps/4800bps/9600bps）in coin acceptor
parameter A2.

When using and testing different coin or bill acceptors the serial setup gets mixed up easy. It is expected behavour. It is not a bug or an issue.

Use: SERIAL_8E1 with DG600F

Thank you. Great DIY

chill117, 2021-11-11:
Thank you for bringing this to our attention. I will review the DG600F's manual and try my build with the suggested change.

relcead, 2021-11-11:
Thank you for your work.

chill117, 2022-03-25:
Tested and works w/ my hardware build. I've committed the change to the master branch. Thanks again!

Closed 2022-03-25.

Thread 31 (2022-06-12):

Battery power

chill117, 2022-06-12:
Add instructions to power the DIY build from a battery. Considerations:
* 12V DC is required for the HX616 or DG600F coin acceptor
* 5V is required to power the ESP32 devkit via its micro USB port

The recommended build design should make it difficult (or impossible) to power the ESP32 from multiple sources simultaneously because this can damage the ESP32 and possibly also a computer (if connected).

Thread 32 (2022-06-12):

Power saving mode (deep sleep / turn off TFT backlight)

chill117, 2022-06-12:
Once #31 is implemented, it will be important to introduce power saving features. When the device is not in use for 30 seconds, put the device into sleep mode. Pressing the button should wake the device.
* Use ESP32's deep sleep mode when on battery power
* Turn off the TFT backlight when on USB power

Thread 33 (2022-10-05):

Make install error due to platformio/framework-arduinoespressif32

ThomasFarstrike, 2022-10-05:
I downloaded and installed the latest platformio and got this build error when doing make install on Debian Linux:

```
user@pc:~/sources/bleskomat-diy$ make
platformio lib install
******************************************************************************************************************************************************************************************************************
If you like PlatformIO, please:
- follow us on Twitter to stay up-to-date on the latest project news > https://twitter.com/PlatformIO_Org
- star it on GitHub > https://github.com/platformio/platformio
- try PlatformIO IDE for embedded development > https://platformio.org/platformio-ide
******************************************************************************************************************************************************************************************************************

WARNING: This command is deprecated and will be removed in the next releases.                                                                                                                             
Please use `pio pkg install` instead.                                                                                                                                                                     
                                                                                                                                                                                                          
Resolving bleskomat32 dependencies...
Platform Manager: Installing espressif32 @ 4.3.0
Downloading  [####################################]  100%
Unpacking  [####################################]  100%
Platform Manager: espressif32@4.3.0 has been installed!
Tool Manager: Installing espressif/toolchain-xtensa-esp32 @ 8.4.0+2021r2-patch3
Downloading  [####################################]  100%  
Unpacking  [####################################]  100%  
Tool Manager: toolchain-xtensa-esp32@8.4.0+2021r2-patch3 has been installed!
Tool Manager: Installing platformio/framework-arduinoespressif32 @ 3.20003.0
Error: Could not find the package with 'platformio/framework-arduinoespressif32 @ 3.20003.0' requirements for your system 'linux_x86_64'
make: *** [Makefile:24: install] Error 1

```

The fix was to just delete that whole platform_packages section:

```
user@pc:~/sources/bleskomat-diy$ git diff
diff --git a/platformio.ini b/platformio.ini
index 5864df3..60764e0 100644
--- a/platformio.ini
+++ b/platformio.ini
@@ -58,8 +58,6 @@ build_flags =
 board = esp32dev
 platform = espressif32@4.3.0
 framework = arduino
-platform_packages =
-       platformio/framework-arduinoespressif32 @ 3.20003.0
 upload_speed = 921600
 ; https://docs.espressif.com/projects/esp-idf/en/latest/esp32/api-guides/partition-tables.html
 board_build.partitions = no_ota.csv

```

And then it worked fine:

```
user@pc:~/sources/bleskomat-diy$ make
platformio lib install

WARNING: This command is deprecated and will be removed in the next releases.                                                                                                                             
Please use `pio pkg install` instead.                                                                                                                                                                     
                                                                                                                                                                                                          
Resolving bleskomat32 dependencies...
Tool Manager: Installing platformio/framework-arduinoespressif32 @ ~3.20003.0
Downloading  [####################################]  100%  
Unpacking  [####################################]  100%  
Tool Manager: framework-arduinoespressif32@3.20003.220626 has been installed!
Tool Manager: Installing platformio/tool-esptoolpy @ ~1.30300.0
Downloading  [####################################]  100%
Unpacking  [####################################]  100%
Tool Manager: tool-esptoolpy@1.30300.0 has been installed!
Library Manager: Installing git+https://github.com/chill117/QRCode.git#v0.0.2
git version 2.20.1
Cloning into '/home/user/.platformio/.cache/tmp/pkg-installing-cinm8dlw'...
remote: Enumerating objects: 24, done.
remote: Counting objects: 100% (24/24), done.
remote: Compressing objects: 100% (19/19), done.
remote: Total 24 (delta 2), reused 17 (delta 2), pack-reused 0
Unpacking objects: 100% (24/24), done.
Note: checking out 'c2f298164aba30c16471b21d1c1c5af8b0bf2a18'.

You are in 'detached HEAD' state. You can look around, make experimental
changes and commit them, and you can discard any commits you make in this
state without impacting any branches by performing another checkout.

If you want to create a new branch to retain commits you create, you may
do so (now or later) by using -b with the checkout command again. Example:

  git checkout -b <new-branch-name>

Library Manager: QRCode@0.0.2+sha.c2f2981 has been installed!
Library Manager: Installing chill1/lnurl @ 0.4.1
Downloading  [####################################]  100%
Unpacking  [####################################]  100%
Library Manager: lnurl@0.4.1 has been installed!
Library Manager: Installing bblanchon/ArduinoJson @ 6.19.4
Downloading  [####################################]  100%
Unpacking  [####################################]  100%
Library Manager: ArduinoJson@6.19.4 has been installed!
platformio platform install espressif32

WARNING: This command is deprecated and will be removed in the next releases.                                                                                                                             
Please use `pio pkg install` instead.                                                                                                                                                                     
                                                                                                                                                                                                          
Platform Manager: espressif32@4.3.0 is already installed
Tool Manager: toolchain-xtensa-esp32@8.4.0+2021r2-patch3 is already installed
Tool Manager: tool-esptoolpy@1.30300.0 is already installed

```

chill117, 2022-10-06:
Thanks for reporting this issue. Fixed by changing:
```
platform_packages =
	platformio/framework-arduinoespressif32 @ 3.20003.0
```
To:
```
platform_packages =
	platformio/framework-arduinoespressif32 @ ~3.20003.0
```

Closed 2022-10-06.

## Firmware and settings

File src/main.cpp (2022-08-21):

#include "main.h"

unsigned int buttonDelay;

void setup() {
	Serial.begin(MONITOR_SPEED);
	spiffs::init();
	sdcard::init();
	config::init();
	logger::init();
	logger::write(firmwareName + ": Firmware version = " + firmwareVersion + ", commit hash = " + firmwareCommitHash);
	logger::write(config::getConfigurationsAsString());
	jsonRpc::init();
	screen::init();
	coinAcceptor::init();
	billAcceptor::init();
	button::init();
	buttonDelay = config::getUnsignedInt("buttonDelay");
}

void disinhibitAcceptors() {
	if (coinAcceptor::isInhibited()) {
		coinAcceptor::disinhibit();
	}
	if (billAcceptor::isInhibited()) {
		billAcceptor::disinhibit();
	}
}

void inhibitAcceptors() {
	if (!coinAcceptor::isInhibited()) {
		coinAcceptor::inhibit();
	}
	if (!billAcceptor::isInhibited()) {
		billAcceptor::inhibit();
	}
}

void resetAccumulatedValues() {
	coinAcceptor::resetAccumulatedValue();
	billAcceptor::resetAccumulatedValue();
}

float amountShown = 0;
unsigned long tradeCompleteTime = 0;

void writeTradeCompleteLog(const float &amount, const std::string &signedUrl) {
	std::string msg = "Trade completed:\n";
	msg += "  Amount  = " + util::floatToStringWithPrecision(amount, config::getUnsignedShort("fiatPrecision")) + " " + config::getString("fiatCurrency") + "\n";
	msg += "  URL     = " + signedUrl;
	logger::write(msg);
}

void runAppLoop() {
	coinAcceptor::loop();
	billAcceptor::loop();
	button::loop();
	const std::string currentScreen = screen::getCurrentScreen();
	if (currentScreen == "") {
		screen::showInsertFiatScreen(0);
	}
	float accumulatedValue = 0;
	accumulatedValue += coinAcceptor::getAccumulatedValue();
	accumulatedValue += billAcceptor::getAccumulatedValue();
	if (
		accumulatedValue > 0 &&
		currentScreen != "insertFiat" &&
		currentScreen != "tradeComplete"
	) {
		screen::showInsertFiatScreen(accumulatedValue);
		amountShown = accumulatedValue;
	}
	if (currentScreen == "insertFiat") {
		disinhibitAcceptors();
		if (button::isPressed()) {
			if (accumulatedValue > 0) {
				// Button pushed while insert fiat screen shown and accumulated value greater than 0.
				// Create a withdraw request and render it as a QR code.
				const std::string signedUrl = util::createSignedLnurlWithdraw(accumulatedValue);
				const std::string encoded = util::lnurlEncode(signedUrl);
				std::string qrcodeData = "";
				// Allows upper or lower case URI schema prefix via a configuration option.
				// Some wallet apps might not support uppercase URI prefixes.
				qrcodeData += config::getString("uriSchemaPrefix");
				// QR codes with only uppercase letters are less complex (easier to scan).
				qrcodeData += util::toUpperCase(encoded);
				screen::showTradeCompleteScreen(accumulatedValue, qrcodeData);
				writeTradeCompleteLog(accumulatedValue, signedUrl);
				inhibitAcceptors();
				tradeCompleteTime = millis();
			}
		} else {
			// Button not pressed.
			// Ensure that the amount shown is correct.
			if (amountShown != accumulatedValue) {
				screen::showInsertFiatScreen(accumulatedValue);
				amountShown = accumulatedValue;
			}
		}
	} else if (currentScreen == "tradeComplete") {
		inhibitAcceptors();
		if (button::isPressed() && millis() - tradeCompleteTime > buttonDelay) {
			// Button pushed while showing the trade complete screen.
			// Reset accumulated values.
			resetAccumulatedValues();
			amountShown = 0;
			screen::showInsertFiatScreen(0);
			logger::write("Screen cleared");
		}
	}
}

void loop() {
	logger::loop();
	jsonRpc::loop();
	if (!jsonRpc::hasPinConflict() || !jsonRpc::inUse()) {
		runAppLoop();
	}
}

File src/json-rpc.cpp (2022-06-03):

#include "json-rpc.h"

namespace {

	uint32_t initTime;
	const uint32_t maxInitialMessageWaitTime = 3000;// milliseconds
	bool sentWaitingMessage = false;
	bool receivedMessage = false;
	bool timedOut = false;

	// https://arduinojson.org/
	// https://www.jsonrpc.org/specification
	const char* jsonRpcVersion = "2.0";

	std::string escapeLine(const std::string &line) {
		const unsigned int numBytes = line.size();
		const unsigned int remainderNumBytes = numBytes % 256;
		const unsigned int allocateNumBytes = remainderNumBytes > 0 ? (numBytes + 256) - remainderNumBytes : numBytes;
		DynamicJsonDocument docLine(allocateNumBytes + 256);
		docLine.set(line);
		String output;// Buffer the serialized JSON string.
		serializeJson(docLine, output);
		std::string escaped = std::string(output.c_str()).substr(1);// Remove first double-quote character.
		escaped.pop_back();// Remove last double-quote character.
		escaped += "\\n";// Escaped line-break character.
		return escaped;
	}

	class JsonRpcError : public std::exception {
		public:
			JsonRpcError(const std::string &t_message) noexcept;
			virtual ~JsonRpcError() = default;
			virtual const char* what() const noexcept override;
		private:
			std::string message;
	};

	JsonRpcError::JsonRpcError(const std::string &t_message) noexcept : message(t_message) {}

	const char* JsonRpcError::what() const noexcept {
		return this->message.c_str();
	}

	void onMessage(const std::string &message) {
		std::string id;
		std::string method;
		try {
			if (message == "" || message.substr(0, 1) != "{") return;
			if (!receivedMessage) {
				logger::write("JSON-RPC serial interface active");
				receivedMessage = true;
			}
			// !! Important !!
			// Keep the JsonDocument instance until done reading from the deserialized document; more info:
			// https://arduinojson.org/v6/issues/garbage-out/
			DynamicJsonDocument docIn(8192);
			const DeserializationError deserializationError = deserializeJson(docIn, message);
			if (deserializationError) {
				std::cerr << "deserializeJson error: " << deserializationError.c_str();
				throw JsonRpcError("Invalid JSON");
			}
			const JsonObject data = docIn.as<JsonObject>();
			if (!data.containsKey("jsonrpc")) {
				throw JsonRpcError("Missing required attribute: \"jsonrpc\"");
			}
			const std::string jsonrpc = data["jsonrpc"].as<const char*>();
			if (jsonrpc != "2.0") {
				throw JsonRpcError("Invalid attribute (\"jsonrpc\"): Only JSON-RPC version 2.0 is supported");
			}
			if (!data.containsKey("id")) {
				throw JsonRpcError("Missing required attribute: \"id\"");
			}
			id = data["id"].as<const char*>();
			method = data["method"].as<const char*>();
			if (method == "") {
				throw JsonRpcError("\"method\" is required");
			}
			logger::write("JSON-RPC command received: " + method);
			if (method == "restart") {
				logger::write("Restarting...");
				DynamicJsonDocument docOut(512);
				docOut["jsonrpc"] = jsonRpcVersion;
				docOut["id"] = id;
				docOut["result"] = true;
				serializeJson(docOut, Serial);
				Serial.println();
				delay(500);// wait before restarting...
				esp_restart();
			} else if (method == "echo") {
				const std::string text = data["params"][0].as<const char*>();
				DynamicJsonDocument docOut(1024);
				docOut["jsonrpc"] = jsonRpcVersion;
				docOut["id"] = id;
				docOut["result"] = text;
				serializeJson(docOut, Serial);
				Serial.println();
			} else if (method == "getinfo") {
				DynamicJsonDocument docOut(1024);
				docOut["jsonrpc"] = jsonRpcVersion;
				docOut["id"] = id;
				DynamicJsonDocument docInfo(768);
				docInfo["firmwareName"] = firmwareName;
				docInfo["firmwareCommitHash"] = firmwareCommitHash;
				docInfo["firmwareVersion"] = firmwareVersion;
				docInfo["spiffsInitialized"] = spiffs::isInitialized();
				docOut["result"] = docInfo;
				serializeJson(docOut, Serial);
				Serial.println();
			} else if (method == "getconfig") {
				DynamicJsonDocument docOut(8192);
				docOut["jsonrpc"] = jsonRpcVersion;
				docOut["id"] = id;
				docOut["result"] = config::getConfigurations();
				serializeJson(docOut, Serial);
				Serial.println();
			} else if (method == "setconfig") {
				logger::write("Saving configurations...");
				config::saveConfigurations(data["params"].as<JsonObject>());
				DynamicJsonDocument docOut(512);
				docOut["jsonrpc"] = jsonRpcVersion;
				docOut["id"] = id;
				docOut["result"] = true;
				serializeJson(docOut, Serial);
				Serial.println();
			} else if (method == "getlogs") {
				if (!spiffs::isInitialized()) {
					throw JsonRpcError("SPIFFS file system not initialized. Reformat SPIFFS then try again.");
				}
				logger::write("Reading logs from SPIFFS file system...");
				Serial.print(std::string("{\"jsonrpc\":\"" + std::string(jsonRpcVersion) + "\",\"id\":\"" + std::string(id) + "\",\"result\":\"").c_str());
				for (int num = 3; num >= 0; num--) {
					const std::string logFilePath = logger::getLogFilePath(num);
					if (spiffs::fileExists(logFilePath.c_str())) {
						File file = SPIFFS.open(logFilePath.c_str(), FILE_READ);
						if (file) {
							while (file.available()) {
								Serial.print(escapeLine(file.readStringUntil('\n').c_str()).c_str());
							}
							file.close();
						}
					}
				}
				Serial.println(std::string("\"}").c_str());
			} else if (method == "deletelogs") {
				if (!spiffs::isInitialized()) {
					throw JsonRpcError("SPIFFS file system not initialized. Reformat SPIFFS then try again.");
				}
				logger::write("Deleting log files...");
				for (int num = 3; num >= 0; num--) {
					const std::string logFilePath = logger::getLogFilePath(num);
					if (spiffs::fileExists(logFilePath.c_str())) {
						spiffs::deleteFile(logFilePath.c_str());
					}
				}
				logger::write("Log files deleted");
				DynamicJsonDocument docOut(512);
				docOut["jsonrpc"] = jsonRpcVersion;
				docOut["id"] = id;
				docOut["result"] = true;
				serializeJson(docOut, Serial);
				Serial.println();
			} else if (method == "spiffs_reformat") {
				logger::write("Reformatting SPIFFS file system...");
				if (!SPIFFS.format()) {
					throw JsonRpcError("Failed to reformat SPIFFS file system");
				}
				logger::write("SPIFFS file system reformatted");
				DynamicJsonDocument docOut(512);
				docOut["jsonrpc"] = jsonRpcVersion;
				docOut["id"] = id;
				docOut["result"] = true;
				serializeJson(docOut, Serial);
				Serial.println();
			} else {
				throw JsonRpcError("Unknown method");
			}
		} catch (const JsonRpcError &e) {
			DynamicJsonDocument docOut(512);
			docOut["jsonrpc"] = jsonRpcVersion;
			if (id != "") {
				docOut["id"] = id;
			}
			docOut["error"] = e.what();
			serializeJson(docOut, Serial);
			Serial.println();
			if (method != "") {
				logger::write("JSON-RPC Error (" + method + "): " + std::string(e.what()), "error");
			} else {
				logger::write("JSON-RPC Error: " + std::string(e.what()), "error");
			}
		} catch (const std::exception &e) {
			DynamicJsonDocument docOut(512);
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

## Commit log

2020-04-20 SublimeText3 + Deviot package alternative to Arduino IDE
2020-09-26 Update wiring diagram (extra ground + fixup TFT)
    Added notes about extra ground, powering options and warning
2020-09-30 UX flow
2020-10-14 Add information about misleading PIN G23 (its twice on the board) (#12)
    * Add information about misleading PIN G23 (its twice on the board)
2020-11-14 Now possible to set USB device path for monitor and upload tasks
    Note about switches on coin acceptor
2020-11-15 Load config from SD card slot on TFT (#14)
    * add feature for uploading config from sdcard
    * improve the config and file IO handling
    * restructure config code
    * add Makefile recipe to create default config
    * update README.md with the sdcard information
    * Rebased with latest master, use SD module
    * Working again (with TFT SD card)
    * Minor cleanup, print card info, mountpoint variable
    * Script to generate bleskomat.conf with readme instructions
    * Tabs instead of spaces
    * Fixup make config task
    [main.cpp]
2021-08-16 Rename connecting cables to jumper wires
2021-08-19 Connecting cable to jumper wire
2021-11-01 Wait for 2 seconds to avoid pressing button multiple times and losing the QR code by an accident
    [main.cpp]
2021-11-11 Create new UK parts list (#22)
    * Create new UK parts list
    * Change to TFT display supplier
    * Updated 10k ohm resistor supplier
    * Changed DC 5.5mm/2.1mm adapter supplier
    * Updated supplier for DC 5.5/2.1mm DC DIP adapter
    * Changed suppliers for dc power components
    * Updated microusb cable supplier
    * Updated 2.54mm pins supplier
    * Remove amazon links, replace with links to other shops
2022-03-25 Use SERIAL_8E1 w/ DG600F
    See https://github.com/samotari/bleskomat-diy/issues/24
    [dg600f.cpp]
2022-03-25 For some TFT displays, the 3V3 pin is required
2022-05-17 JSON-RPC via serial
    Use Non-volatile storage (NVS) to save configurations
    Firmware name, version, commit hash
    Use UART1 pins for coin acceptor
2022-05-18 Add STL files for hx616 case
    [door.stl]
2022-05-23 Refactor config, modules
    Button/coin pin and other options now configurable
2022-05-24 Use fixed version numbers: platform, framework
2022-05-27 Use SPIFFS to save log files
    Improved logging
    Button delay: Remove delay(), use elapsed time check instead
2022-05-27 Fixup SD card use
    [main.cpp]
2022-05-28 Fix JSON-RPC init when pin conflict exists
    [json-rpc.cpp]
2022-05-28 Improving logging and error handling in JSON-RPC
    [json-rpc.cpp]
2022-10-10 Debounce hx616 pulse counting to prevent extraneous accumulated value
    Don't count pulses caused by reconnecting coin signal pin
    Or powering on the hx616
    Or changing the physical switches on the hx616
    Still possible but less likely as pulse high/low must be 20-200ms
